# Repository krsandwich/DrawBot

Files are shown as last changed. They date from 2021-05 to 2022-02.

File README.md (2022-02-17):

# Drawbot

This is a parts list and assembly guide for the Lab64 drawbot, a small desktop robot that draws cool pictures for you. 

## Background 
The goal of this project is to build a desktop bot which can hold a pen and use it to draw images on a sheet of paper. Achieving this requires two main components -- the ability to move precisely in the XY plane over the paper, and the ability to lift a pen on and off of the paper. 

- **XY motion**
The XY motion is driven by two Nema-17 stepper motors, one mounted to each end of the x axis. [Here](https://www.youtube.com/watch?v=_nzxGOKhHSY ) is a visualization of how driving the stepper motors in sync and against each other allows the carriage to move in 3D.

- **Pen lifting**
The lifting of the pen is driven by a tiny SG90 servo. The pen will drop down by gravity when the servo is not blocking it. To lift the pen up, the servo rotates, lifting the pen-holder up and moving the pen off the paper. 

## Parts list

### Tools & Bolts
|  Item No  |  Qty / kit |  Description |  Link |
| :--- | :--- | :--- | :--- |
| 1 | 1 | Metric m5 allen key | [Amazon](https://www.amazon.com/Eklind-14610-Long-Hex-L-Key/dp/B000GAOAFK/)  |
| 2 | 1 | M5 bolt + nut set | [Amazon](https://www.amazon.com/DYWISHKEY-Pieces-Stainless-Steel-Button/dp/B07WZHN2XS/) |
| 3 | 12 | M5 t-nuts | [Amazon](https://www.amazon.com/100Pcs-T-Nuts-Carbon-Nickel-Plated-Sliding/) |

### Hardware
|  Item No  |  Qty / kit |  Description |  Link |
| :--- | :--- | :--- | :--- |
| 4 | 1 | Openbuilds 20x40x500 v-slot | [Openbuilds](https://openbuildspartstore.com/v-slot-20x40-linear-rail/) |
| 5 | 1 | Openbuilds 20x20x250 v-slot | [Openbuilds](https://openbuildspartstore.com/v-slot-20x20-linear-rail/) |
| 6 | 6 | V-slot wheels | [Amazon](https://www.amazon.com/AFUNTA-Plastic-Bearings-Printer-Compatible/dp/B07KPWJ3ZC/) |
| 7 | 5 | Bearings **could be 3d printable | [Amazon](https://www.amazon.com/gp/product/B07JMRR7CC/) |
| 8 | 1 | GT2 belt | [Amazon](https://www.amazon.com/Upgrade-Non-Slip-Abrasion-Resistance-Printers/dp/B08NVL55HC/) |

### Electronics
|  Item No  |  Qty / kit |  Description |  Link |
| :--- | :--- | :--- | :--- |
| 9 | 1 | Elegoo uno board | [Amazon](https://www.amazon.com/ELEGOO-Board-ATmega328P-ATMEGA16U2-Compliant/dp/B01EWOE0UU/) |
| 10 | 2 | Nema17 stepper motor | [Amazon](https://www.amazon.com/RTELLIGENT-Stepper-Bipolar-42x42x38mm-42A02C-XH2-54/dp/B0817TGDQM/?th=1) |
| 11 | 2 | A4988 stepper driver | [Amazon](https://www.amazon.com/ARCELI-Compatible-Stepper-StepStick-Controller/dp/B07MXXL2KW) |
| 12 | 1 | Towerpro micro servo | [Amazon](https://www.amazon.com/Smraza-Helicopter-Airplane-Control-Arduino/dp/B07L2SF3R4/ ) |
| 13 | 1 | Jumper wire | [Amazon](https://www.amazon.com/EDGELEC-Breadboard-Optional-Assorted-Multicolored/dp/B07GD431C1/) |
| 14 | 1 | Breadboard | [Amazon](https://www.amazon.com/Breadborad-Solderless-Breadboards-Distribution-Connecting/dp/B082VYXDF1/) |
| 15 | 2 | 9V battery | [Amazon](https://www.amazon.com/Energizer-Alkaline-Volt-Batteries-Count/dp/B01AVK3NMU/) |
| 16 | 2 | Battery hats | [Amazon](https://www.amazon.com/Battery-Connector-Leather-Housing-Connection/dp/B06X8YZJ64/) |

### 3D Prints
|  Item No  |  Qty / kit |  Description | 
| :--- | :--- | :--- |
| 17 | 2 | Stepper mount | 
| 18 | 2 | GT2 pulley for stepper | 
| 19 | 1 | Lower cart |
| 20 | 1 | Upper cart | 
| 21 | 4 | Cart spacers |
| 22 | 4 | Pulley spacers |
| 23 | 1 | Back pulley |
| 24 | 1 | Servo mount | 
| 25 | 1 | Pen mount |
| 26 | 1 | Belt clamp | 

## Mechanical Assembly

If you're coming here from the recent workshop, these instructions will be in a different order than you may remember. I recommend following these instructions from the start, and you may find that you've already done some steps as you go. 

These instructions may be difficult to follow in places -- I don't have enough photos, and don't have enough bolts to recreate the bot to take the photos. If you have trouble, we'll be having a second catcup-up mechanical session while people with the mechanics completed work on the electronics (electronics are far easier to complete on your own)

### Bolts
Your kit has the following bolts:
|  Item  |  Qty / kit |  Description | 
| :--- | :--- | :--- |
| M5 T-Nuts | 8 + 5 extra | Silvery oblong nuts with a hole in the middle | 
| M5 hex nuts | 7 + 5 extra | Hexagonal nuts with a hole in the middle | 
| M5x10 bolts | 8 | Shortest size |
| M5x12 bolts | 6 | Second-shortest (very hard to differentiate from M5x10s, be careful!) | 
| M5x16 bolts | 8 | Second-longest |
| M5x20 bolts | 6 OR 12 | Longest size |
| M5 allen key | 1 | Allen key used to screw in bolts |

Begin by sorting your bolts. It's okay if you have one more or less of each type.

### Stepper motor
Begin with the 2 Nema 17 stepper motors, 2 GT2 pulleys, and 2 stepper mounts (pictured below). To push the pulley onto the motor, look closely at the stepper motor axle and notice that they are not perfectly round, they have one flat edge. Line up that flat edge with the flat edge on the 3d printed pulley, flip the whole thing upside down, and push down hard against a flat object until the pulley is flush with the axle. Then, take the stepper mount. Orient the long side in the same direction as the stepper motor wires, and push until it snaps into place. It should hold without any screws. 

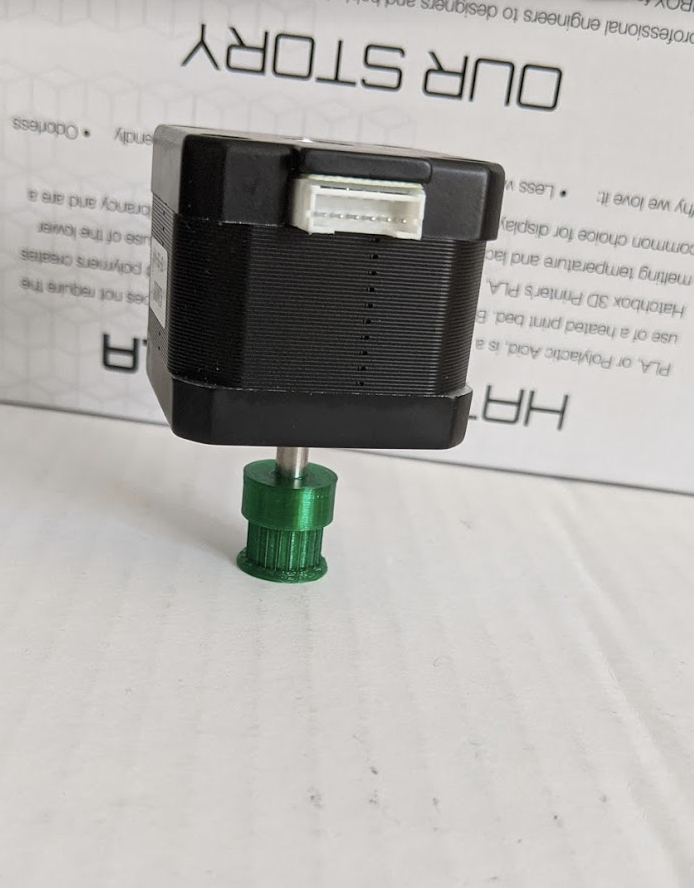
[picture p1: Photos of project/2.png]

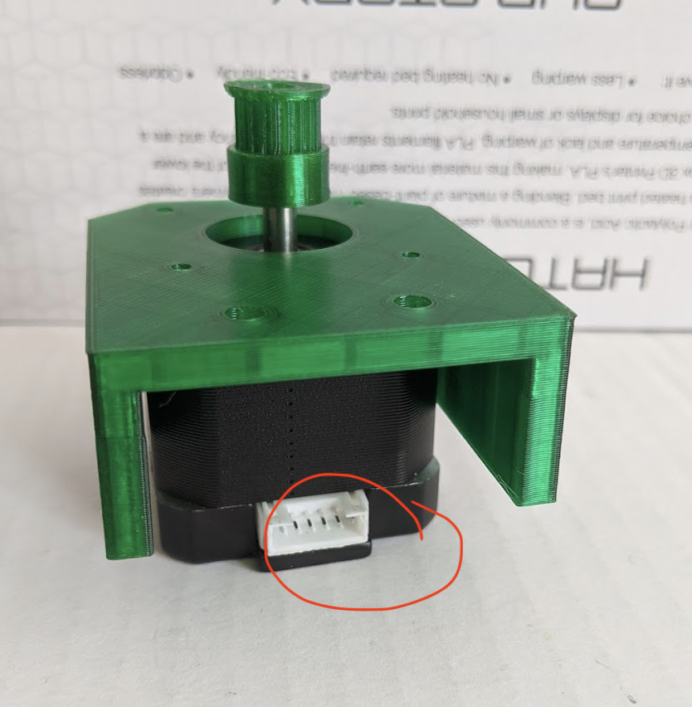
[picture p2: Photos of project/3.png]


### Main carriage
Select 6 M5x20s (20 mm long 5mm bolts), 6 M5 hex nuts, the black wheels, and the two round 3d printed carts. There are hexagonal holes on the insides of the carts, opposite the square lumps -- press the nuts in, they should snap into place. Flip the cart over and attach the wheels to the lumps with the M5x20s. You should leave the bolts just slightly loose; make sure that all wheels can spin freely.

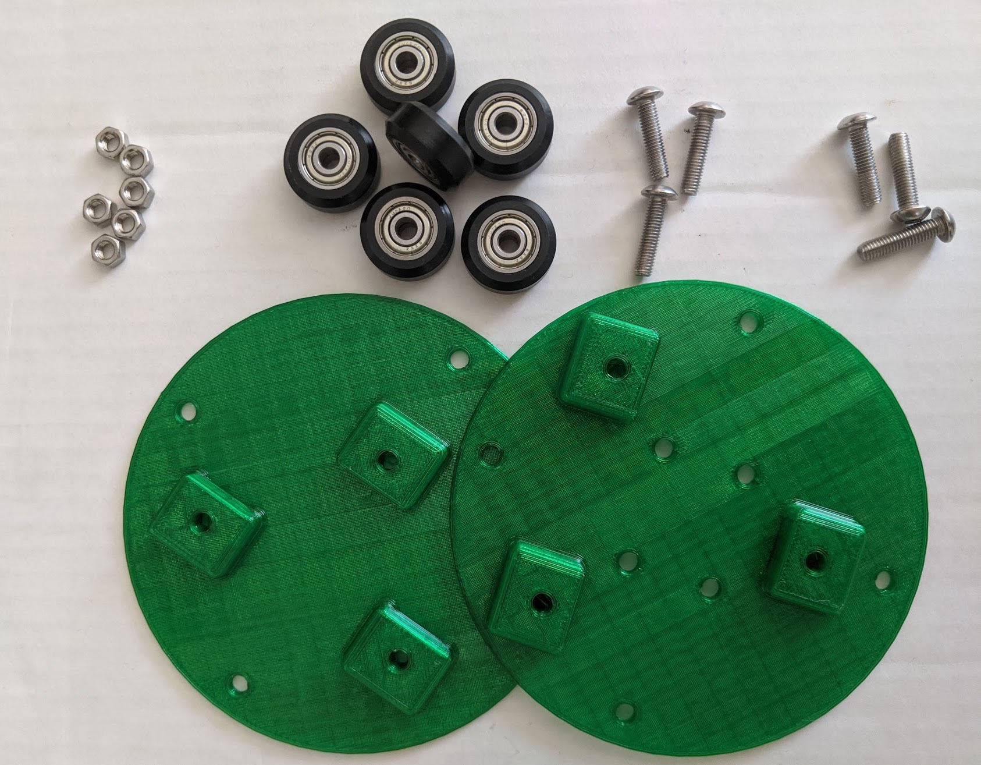
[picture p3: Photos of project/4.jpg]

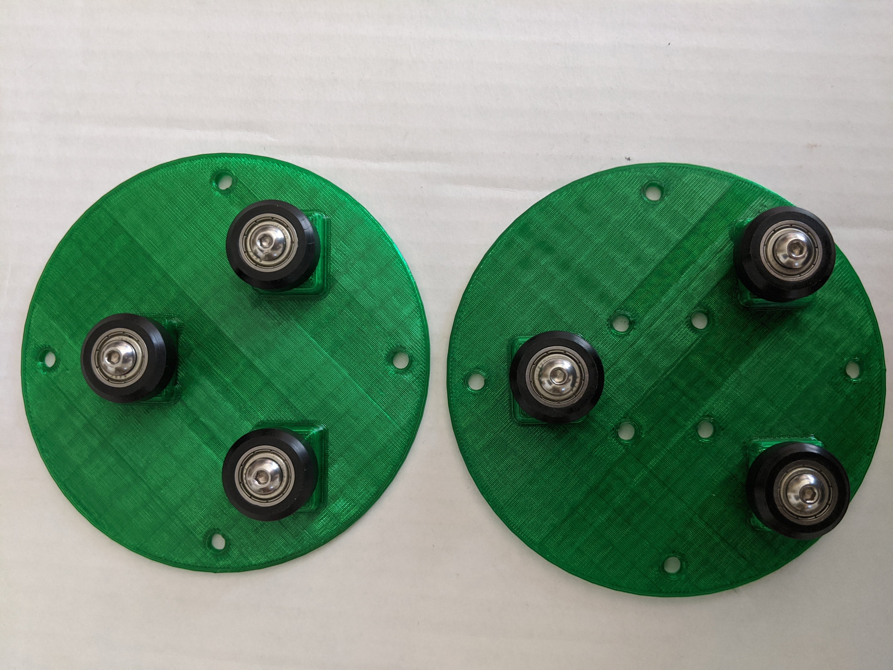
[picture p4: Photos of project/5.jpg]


One of the carts has four holes in the centre. The one with the holes is the lower cart, and the other is the upper cart. Take the lower cart, and insert four M5x12s through the center 4 holes, passing from the lumpy side to the inside (bolt head stays on the lumpy side). These will be used to hold pulleys. Slide the tiny spacers onto the M5x12s from the inside of the cart, with the slightly wider side down presing against it.  

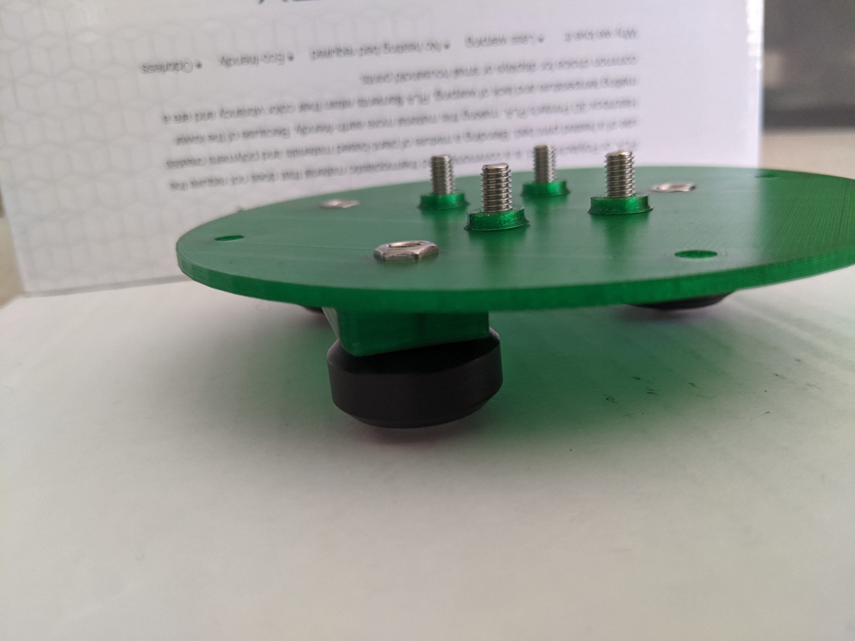
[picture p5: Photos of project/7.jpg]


Next, you will put in the spacers using four M5x16 bolts, as pictured. Once this is done, place the metal pulleys onto the middle M5x12s. You can then pick up the top cart and place it onto the bottom one. Tighten the M5x16s to connect. 

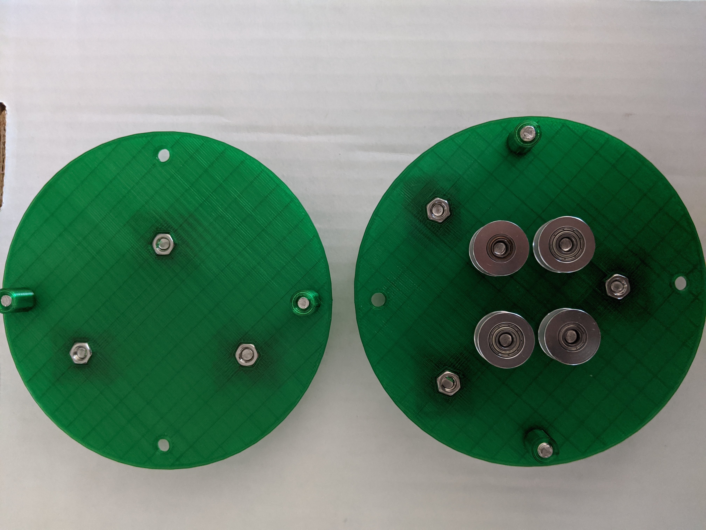
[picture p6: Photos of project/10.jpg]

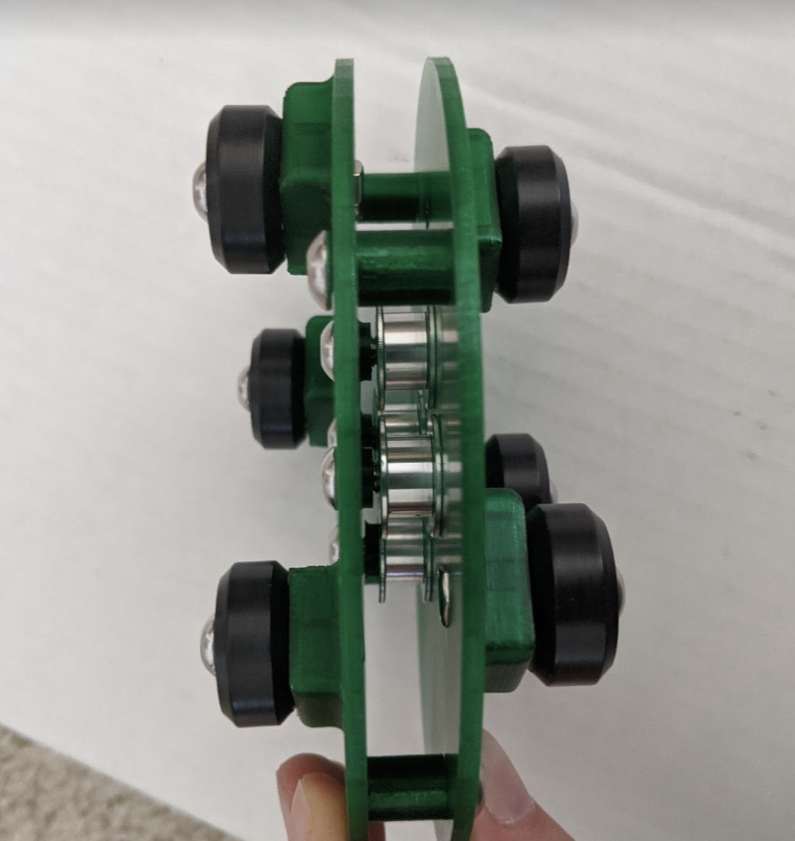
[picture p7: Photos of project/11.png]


### Attaching to metal
You will use small metal t-nuts in order to attach to the metal extrusion. The t-nuts will fit into the slots in the metal, and you will be able to put a M5x10 bolt through and tighten it to create a strong attachment. Begin with one of the stepper motors, and put two M5x10s through the holes. Then, thread the t-nuts ever-so-slightly on as pictured. Slide the larger piece of aluminum extrusion into the t-nuts, and tighten them down. They should create a firm attachment. If they do not, loosen them and try again -- it may take a few tries and some practice. When you're done, you will be able to shake pieces around and have it hold solidly without slipping at all. 

Then, you can roll the carriage onto the extrusion. Push the smaller piece of extrusion onto the upper cart. After the carriage is rolled onto the lower extrusion, you can attach the second stepper motor. 

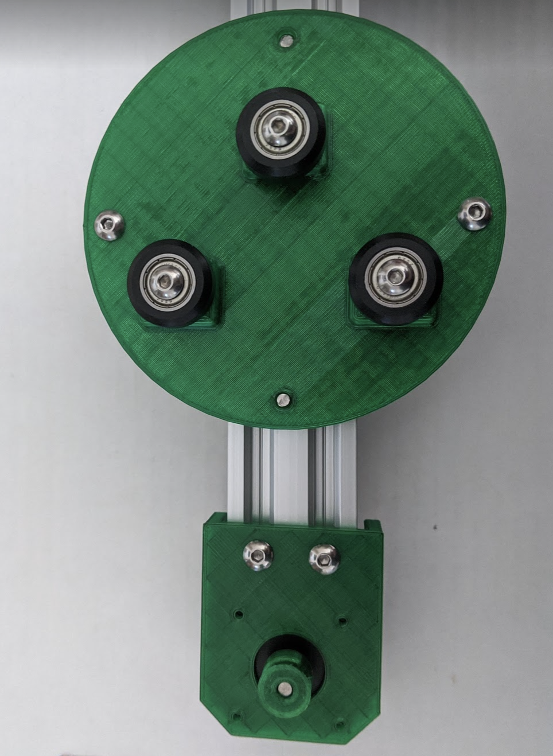
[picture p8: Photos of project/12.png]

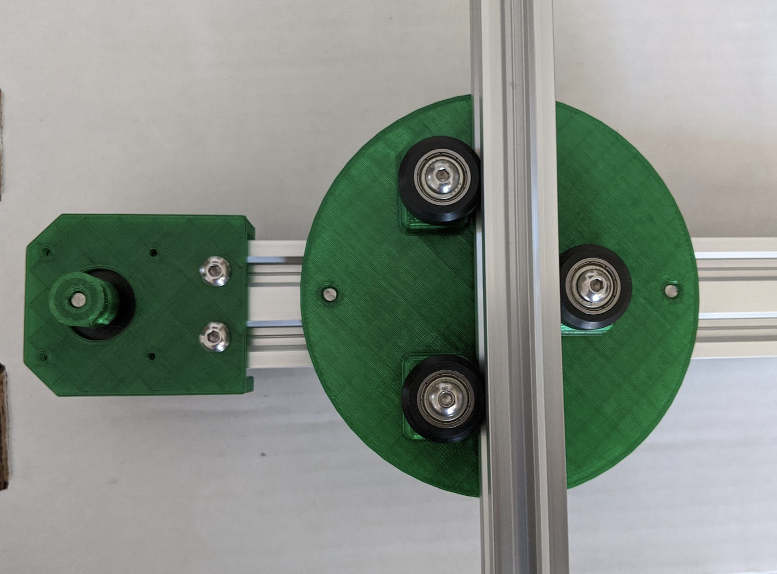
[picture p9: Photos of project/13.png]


### Attaching back pulley
Attach the last metal pulley to the U-shaped back pulley piece, with a M5x16 bolt passing loosely through the print from below up into the pulley. Then use the same strategy with the t-nuts and two M5x10s to attach the U-shaped back pulley piece to the small piece of metal extrusion. There are four potential holes you can use; I recommend just starting with two bolts diagonally across from each other. 
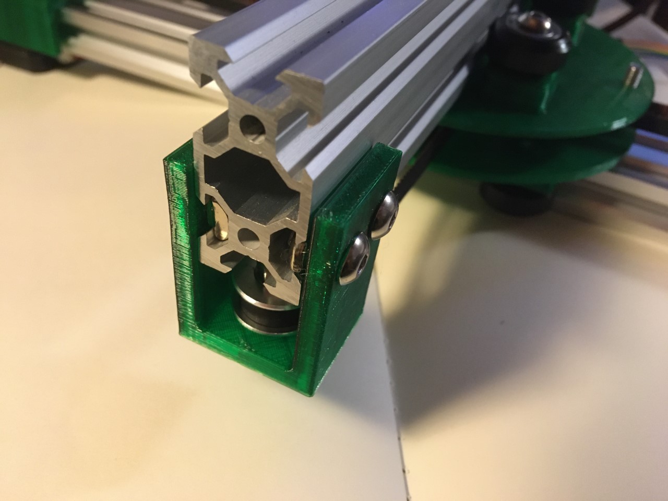
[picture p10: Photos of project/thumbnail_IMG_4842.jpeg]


### Pen mount
Begin by attaching the servo (in blue, in the photo) to the pen mount (in yellow). You can use the tiny pointy bolts that come with the servo bag, and use your fingers to tighten it as much as you can. Then affix the pen mount (in yellow) to the metal, using 2M5x10s, 2 t-nuts and the same procedure you just used for the back pulley. Next, you will run the belt, before completing the pen mount. 

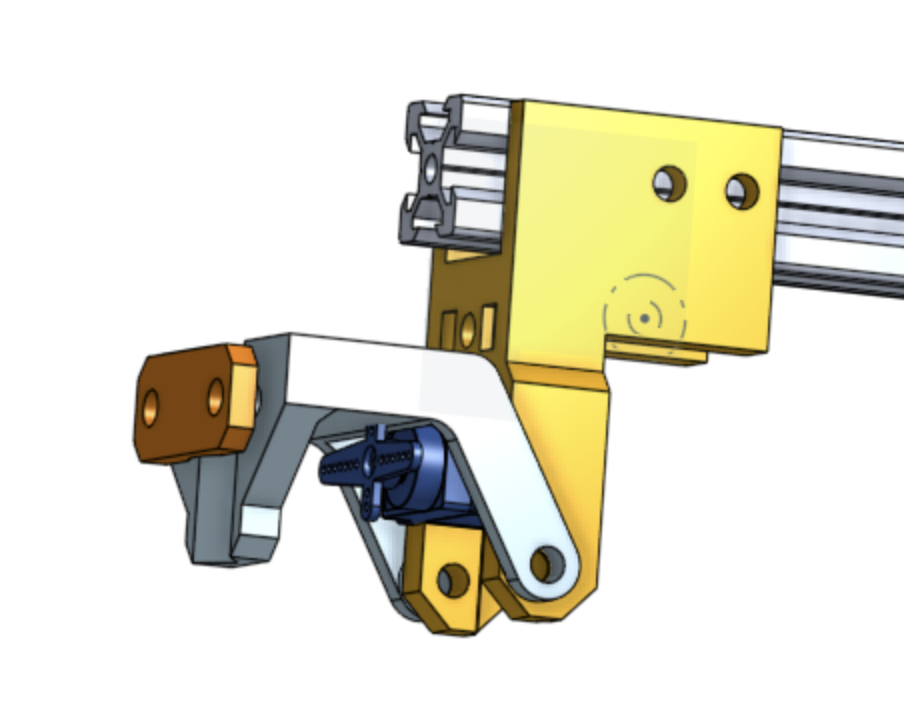
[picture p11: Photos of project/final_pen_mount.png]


### Running the belt
Running the belt is the trickiest part of the assembly. The belt must run around all of the pulleys in a plus sign, to transmit the motion of the steppers into the carriage. Begin by poking one end of the belt into the stepper mount. There are two parallel slots for the belt, slide one end through with the orientation shown in the diagram. Then cut a length of belt, and slide the opposite end into and out of the carriage in the pattern shown. I recommend getting chopsticks, tweezers, or a fork to grab the belt and move it aorund. If this does not work for you, undo the spacer bolts keeping the upper and lower cart together, loop the belt, and reassemble the carriage. Once you're done, pass it through the second slot in the stepper mount, and trim any extra. Tighten down the spiny piece using the center bolt to clamp the belt in place. 

If you hold the pulleys and twist them, the carriage should move. Moving the motors in the same direction will move the carriage left and right, and moving the motors in opposite directions will move the carriage back and forth. 

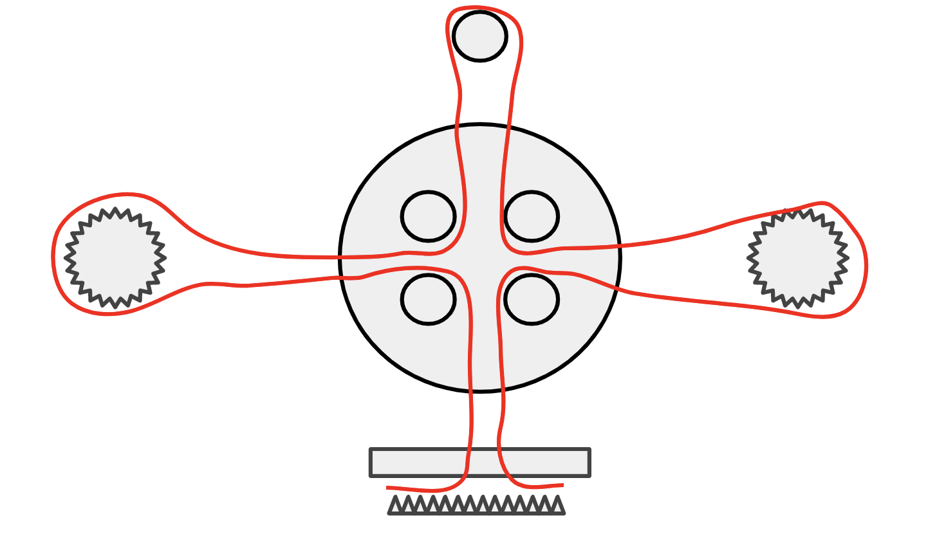
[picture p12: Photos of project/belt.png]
Belt diagram


### Attaching the pen
Attach the pen swivel (in light blue in the image in the Pen Mount section) to the pen mount, using 2 M5x12s. The swivel should be able to rotate up and down when the servo turns. Once you're sure that's in place, take any pencil. Clamp it to the pen swivel using 2 M5x16s, using the pen clamp (orange in the image). 

## Electronics

All electronics will be conected using the breadboard and jumper wires. This is a quick and easy way to prototype mechatronic systems. Full electronics photo TBD. 

### Stepper motors
Breadboards are connected horizontally. Gently push the red A4988 onto a breadboard, with each row of pins on a different half of the board. Make sure that the orientation matches the diagram, and link the wires as pictured. Repeat a second time for the second A4988 and second stepper motor, making sure to connect to pins 3&4 for the first and then 12&13 for the second on the elegoo. 
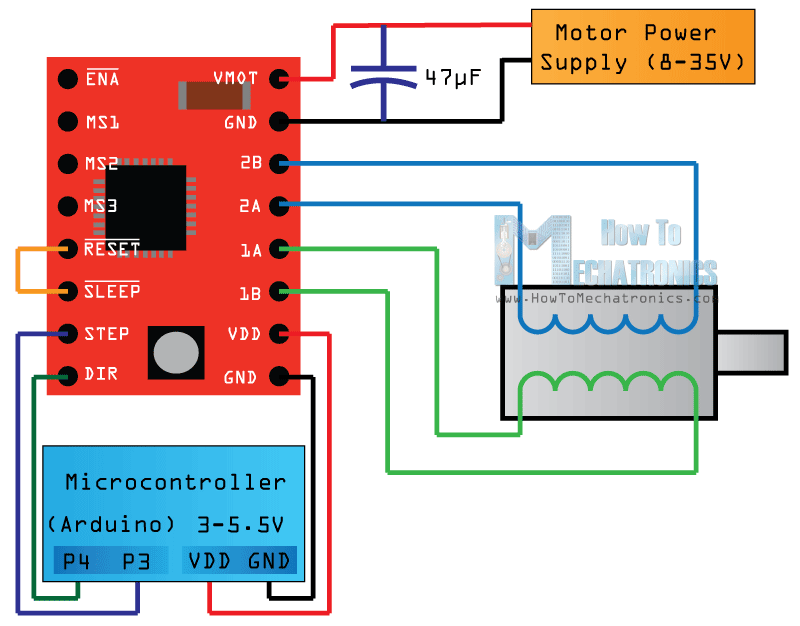
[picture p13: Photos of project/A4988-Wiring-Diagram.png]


### Servo
TBD.

## Code
The Elegoo board can be run directly from the Arduino software. Download the Arduino IDE here: https://www.arduino.cc/en/software

Test that your stepper motors are working by downloading the stepper test code from the "Starter Code" file. It should make your steppers run in a square, wait, and then do it again in an infinite loop. If your stepper motors are screaming and not rotating, please let us know and we can debug.

Now that you have that running, we will upload the real code. Please do the following: <br/>

`git clone https://github.com/krsandwich/DrawBot.git` <br/>
`cd DrawBot/drawbot_code` <br/>
`python3 -m venv .env` <br/>
`source .env/bin/activate` <br/>
`python3 -m pip install -r requirements.txt`<br/><br/>
Now, open drawbot_arduino and run the sketch making sure to specify the correct port for your arduino. Copy down the port name and put it in line 73 of drawbot.py. Now run the following command:<br/><br/>
`
python3 drawbot.py
`<br/><br/>
You will see a hello world graphic pop up! The black lines represent lines that will be drawn and red lines represent movement. Make sure your motors are connected to power (you should hear an annoying buzz) and that the arduino script is running. Now you can close the Hello World window and the drawbot should start drawing!

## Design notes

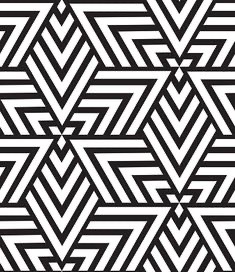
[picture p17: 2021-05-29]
drawbot_code/imgs/lines.jpg

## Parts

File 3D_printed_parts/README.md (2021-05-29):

### 3D Printed Parts



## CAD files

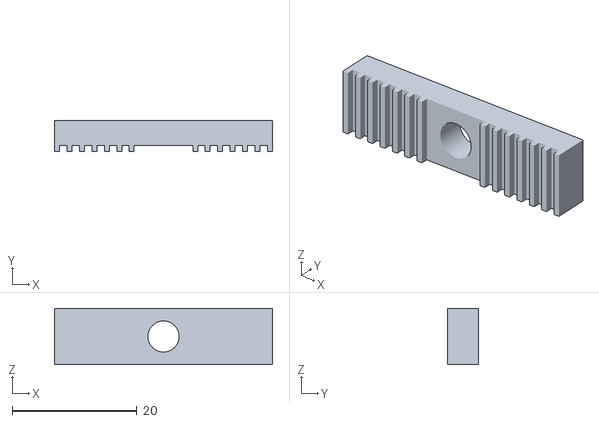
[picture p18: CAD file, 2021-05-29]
3D_printed_parts/GT2_belt_clamp.stl
35.0 x 5.00 x 9.00

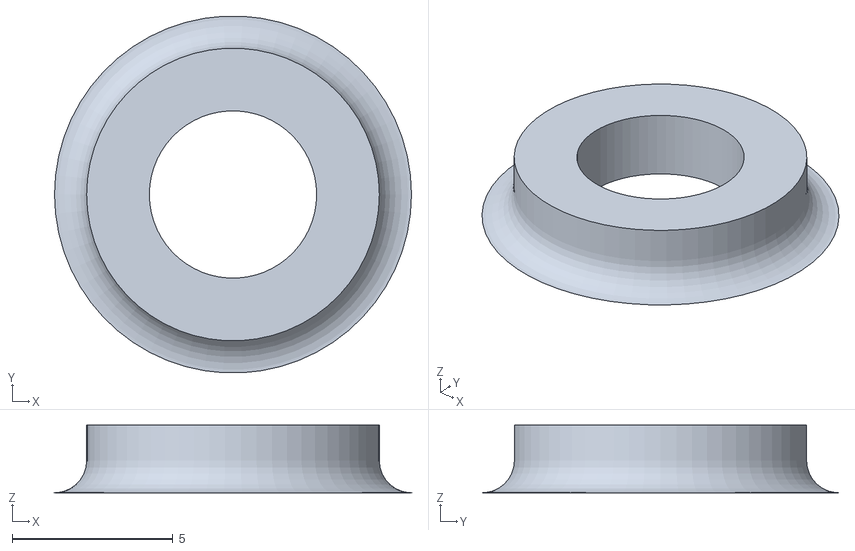
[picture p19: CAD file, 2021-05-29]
3D_printed_parts/Pulley_spacer.stl
11.1 x 11.1 x 2.10

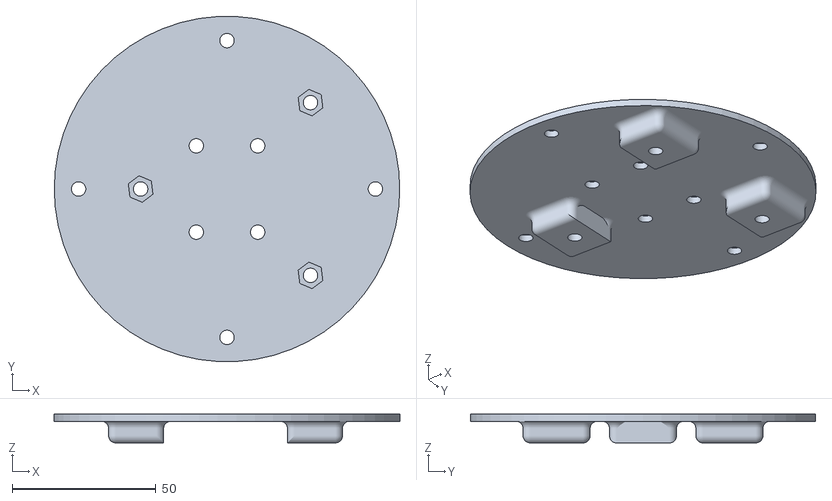
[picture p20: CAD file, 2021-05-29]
3D_printed_parts/Lower_cart.stl
120.0 x 119.8 x 10.0

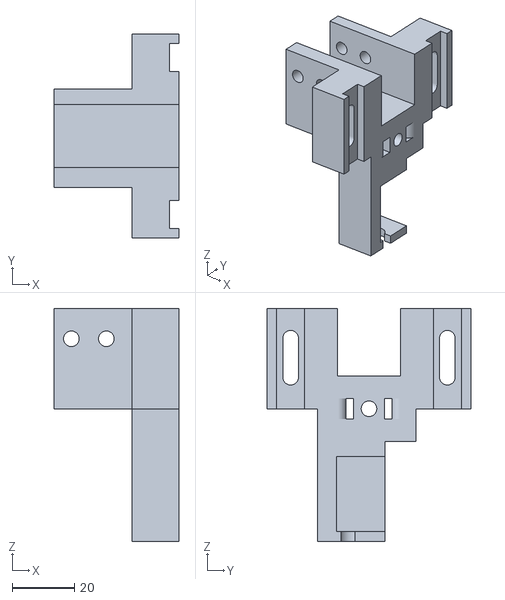
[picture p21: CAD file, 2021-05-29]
3D_printed_parts/Servo_mount.stl
40.0 x 65.2 x 74.6

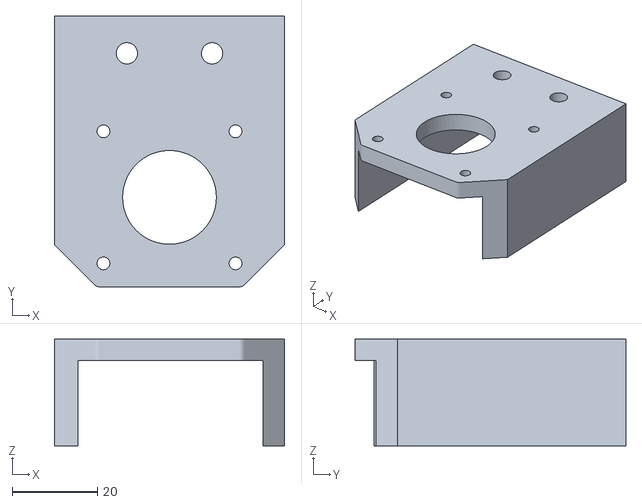
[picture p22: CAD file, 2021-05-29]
3D_printed_parts/Stepper_clamp.stl
54.0 x 63.5 x 25.0

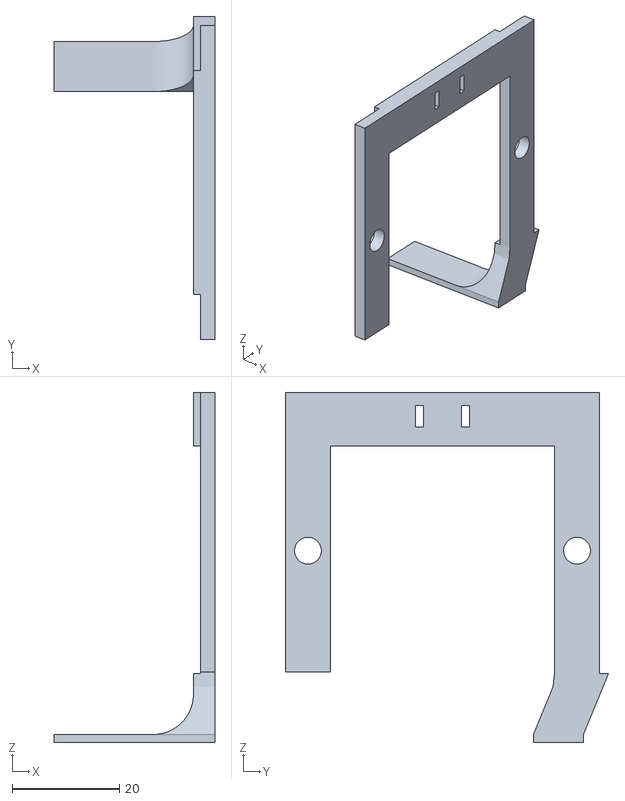
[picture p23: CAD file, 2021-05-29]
3D_printed_parts/Pen_Mount.stl
30.0 x 60.3 x 65.3

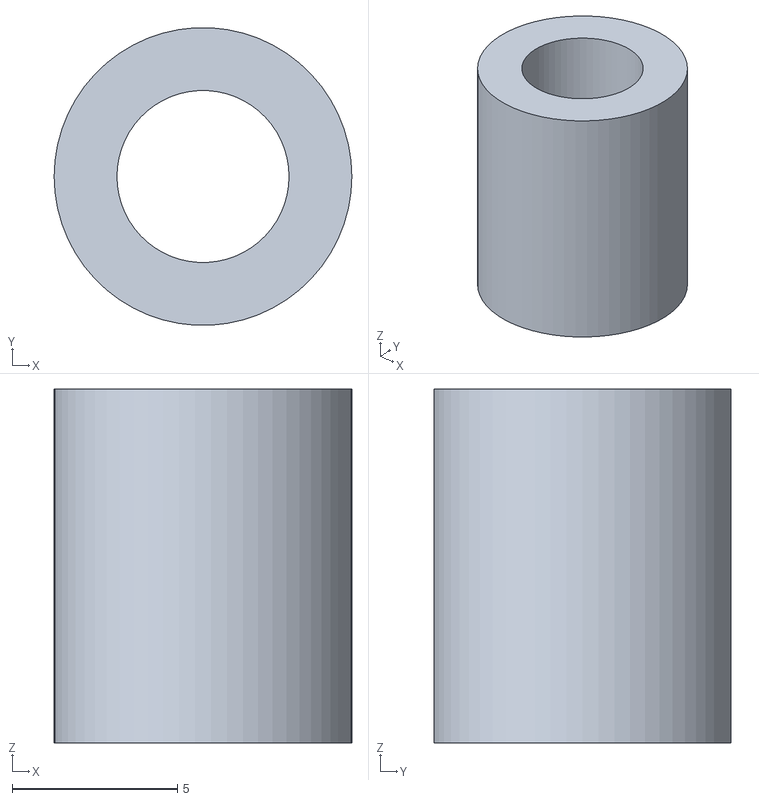
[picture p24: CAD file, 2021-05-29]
3D_printed_parts/Spacer.stl
9.00 x 8.99 x 10.7

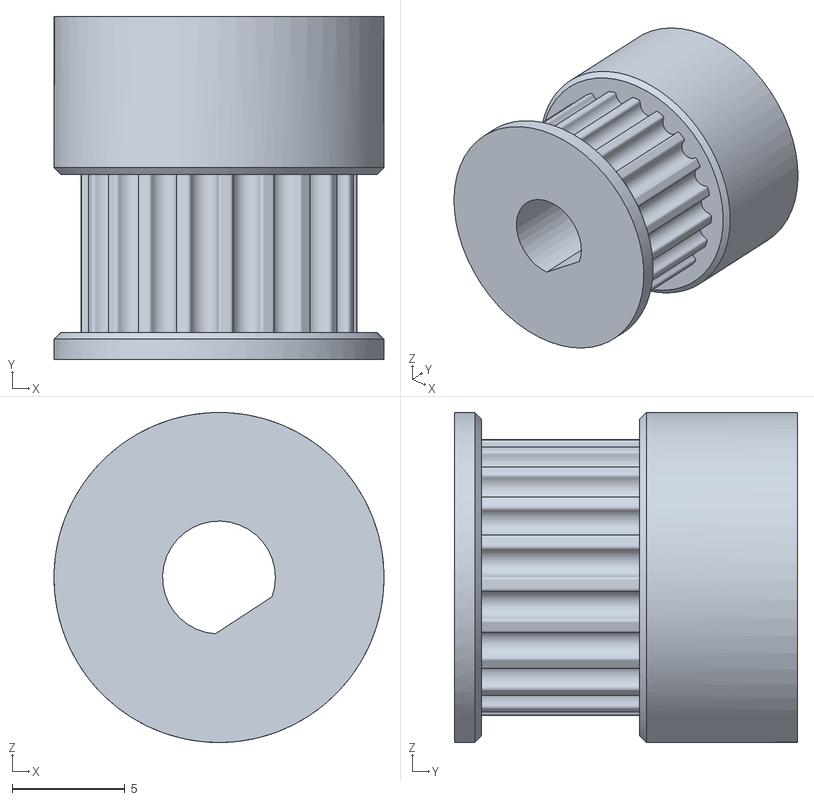
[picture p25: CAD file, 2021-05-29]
3D_printed_parts/GT2_Pulley.stl
14.6 x 15.2 x 14.6

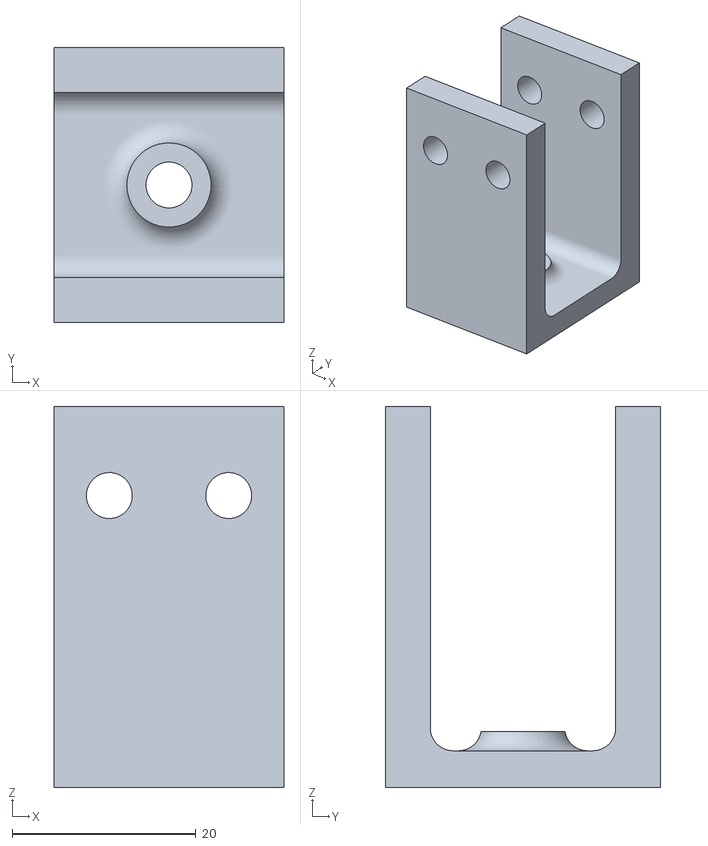
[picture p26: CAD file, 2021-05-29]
3D_printed_parts/Back_pulley.stl
25.0 x 30.0 x 41.5

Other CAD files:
3D_printed_parts/Upper_cart.stl

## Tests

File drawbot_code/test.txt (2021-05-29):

m 20.92268,117.88144 c 0.36974,-0.22427 -0.222948,-3.41363 0,-4.08247 0.07607,-0.22822 0.510309,-0.26975 0.510309,-0.51031 0,-0.24056 -0.510309,-0.26975 -0.510309,-0.51031 0,-0.16455 0.878846,-0.73707 1.020619,-1.02062 0.07607,-0.15214 -0.05379,-0.34893 0,-0.51031 0.124309,-0.37293 0.553521,-1.29738 1.020618,-1.53093 0.114376,-0.0572 1.919972,0 2.041237,0 0.170104,0 -0.680412,0 -0.510309,0 0.340206,0 0.780057,-0.24056 1.020619,0 0.170103,0.17011 -0.568655,0.27693 -0.51031,0.51031 0.516023,2.0641 1.530929,0.87402 1.530929,3.06186 0,0.86736 -0.402727,1.69088 -0.51031,2.55154 -0.0633,0.50637 0,1.02062 0,1.53093 0,1.02062 0,2.04124 0,3.06186 0,3.91237 0,7.82474 0,11.73711 0,0.85052 0,1.70103 0,2.55155 0,0.51031 0.0633,1.02456 0,1.53093 -0.107583,0.86066 -0.299944,1.71008 -0.510309,2.55154 -0.130464,0.52186 -0.44359,0.99717 -0.51031,1.53093 -0.105493,0.84395 0.08463,1.70525 0,2.55154 -0.0863,0.86306 -0.402726,1.69089 -0.510309,2.55155 -0.0633,0.50637 0.123768,1.03586 0,1.53093 -0.222171,0.88868 -0.798448,1.66286 -1.020619,2.55155 -0.123768,0.49507 0,1.02061 0,1.53092 -0.170103,0.51031 -0.340206,1.02062 -0.510309,1.53093 -0.363509,1.09053 -0.860425,2.45081 -1.020618,3.57217 -0.04474,0.3132 0.119786,3.33259 0,3.57216 -0.215166,0.43033 -0.753739,0.6203 -1.020619,1.02062 -0.09436,0.14154 0.05379,0.34893 0,0.51031 -0.120281,0.36084 -0.510309,0.64026 -0.510309,1.02062 0,0.24056 0.402727,0.29514 0.510309,0.51031 0.405643,0.81128 -1.020618,1.05151 -1.020618,1.53093 0,0.1701 0.340206,0 0.510309,0 0,0.3402 0.152145,0.71632 0,1.02061 -0.07607,0.15215 -0.390028,-0.12028 -0.510309,0 -0.120281,0.12028 0,0.68042 0,0.51031 0,-2.69548 -0.360843,-0.7345 0.510309,-2.04123 0.210987,-0.31649 0.282092,-0.71633 0.510309,-1.02062 3.384966,-3.38497 -0.481124,0.96225 1.020619,-2.04124 0.215165,-0.43033 0.841933,-0.57391 1.020618,-1.02062 0.189524,-0.47381 -0.189524,-1.05712 0,-1.53093 0.830745,-0.83074 1.168191,-0.95302 1.530928,-2.04123 0.221787,-0.66536 0.149466,-1.43983 0.510309,-2.04124 0.195695,-0.32616 0.928368,-0.1413 1.020619,-0.51031 0.130463,-0.52185 -0.680412,-1.02062 -0.510309,-1.53093 0.228217,-0.68465 1.20818,-0.88543 1.530927,-1.53093 0.228219,-0.45643 -0.262552,-1.09334 0,-1.53092 0.31555,-0.52592 1.162939,-0.52997 1.530929,-1.02062 0.204123,-0.27217 -0.08251,-0.69057 0,-1.02062 0.09225,-0.36901 0.340207,-0.68041 0.51031,-1.02062 1.850017,-3.70004 -0.537914,0.80687 1.020617,-1.53093 0.210986,-0.31648 0.241353,-0.75166 0.51031,-1.02062 0.268957,-0.26895 0.704138,-0.29932 1.020619,-0.51031 0.600477,-0.40031 0.953577,-1.09791 1.530927,-1.53092 0.304289,-0.22822 0.704138,-0.29933 1.020617,-0.51031 0.170103,-0.1701 0.340207,-0.34021 0.51031,-0.51031 0,-0.1701 -0.12028,-0.39003 0,-0.51031 0.120282,-0.12028 0.358166,0.0761 0.51031,0 0.215164,-0.10758 0.295145,-0.40273 0.510309,-0.51031 0.152144,-0.0761 0.340207,0 0.51031,0 0.340207,0 0.680411,0 1.020617,0 0.170103,0 -0.68041,0 -0.51031,0 0.340207,0 0.680413,0 1.02062,0 0.170103,0 -0.680413,0 -0.51031,0 0.340207,0 0.680413,0 1.02062,0 0.170103,0 -0.390028,-0.12028 -0.51031,0 -0.12028,0.12028 0,0.34021 0,0.51031 0,1.19072 0,2.38144 0,3.57216 0,4.42268 0,8.84537 0,13.26805 0,2.04123 0,4.08247 0,6.12371 0,0.68041 0.08439,1.36608 0,2.04124 -0.08699,0.69593 -0.411123,1.34693 -0.51031,2.04123 -0.07217,0.50518 0.08389,1.02756 0,1.53093 -0.08843,0.53059 -0.404815,1.00346 -0.51031,1.53093 -0.133437,0.6672 0,1.36082 0,2.04123 0,0.85052 0,1.70103 0,2.55155 0,0.34021 0,1.36082 0,1.02062 0,-0.34021 -0.152143,-0.71633 0,-1.02062 0.430332,-0.86066 1.50748,-1.2406 2.04124,-2.04124 0.421973,-0.63296 0.643194,-1.38074 1.020617,-2.04123 0.304289,-0.53251 0.746336,-0.98237 1.020619,-1.53093 0.240562,-0.48113 0.269748,-1.0498 0.51031,-1.53093 0.613315,-1.22663 1.375219,-2.37333 2.041237,-3.57216 0.184718,-0.3325 0.314613,-0.69446 0.510309,-1.02062 0.315548,-0.52592 0.805268,-0.95667 1.020617,-1.53093 0.873438,-2.32916 0.07625,-2.19374 1.02062,-4.08247 0.443574,-0.88715 1.005242,-1.71045 1.530927,-2.55155 0.325056,-0.52009 0.900337,-0.92952 1.020619,-1.53093 0.07459,-0.37297 -0.630589,-0.65978 -0.51031,-1.02062 0.268957,-0.80687 1.150568,-1.28051 1.530927,-2.04123 0.304292,-0.60858 -0.304289,-1.43266 0,-2.04124 0.215167,-0.43033 0.75374,-0.6203 1.02062,-1.02062 0.09436,-0.14154 0,-0.34021 0,-0.51031 0,-0.1701 0,-0.34021 0,-0.51031 0,-0.1701 0,-0.34021 0,-0.51031 0,-0.1701 0.152146,-0.43424 0,-0.51031 -0.456435,-0.22821 -1.02062,0 -1.530927,0 -0.167587,0 -1.454893,-0.0507 -1.530929,0 -1.991204,1.32747 -0.504413,0.49262 -1.020617,2.04124 -0.388477,1.16543 -1.02062,-0.31544 -1.02062,1.53093 0,0.24056 0.51031,0.26975 0.51031,0.51031 0,0.38036 -0.418058,0.65161 -0.51031,1.02062 -0.08251,0.33004 0,0.68041 0,1.02061 0,0.51031 0,1.02062 0,1.53093 0,1.53093 0,3.06186 0,4.59279 0,0.32615 -0.0736,2.91465 0,3.06185 0.51031,1.02062 1.02062,0.76547 1.530927,1.53093 0.869294,1.30394 0.05944,0.93762 1.530929,2.04124 0.608579,0.45643 1.432658,0.56418 2.041237,1.02062 0.340206,0.3402 0.680413,0.68041 1.020619,1.02061 0.170104,0 0.358164,-0.0761 0.510308,0 0.215167,0.10758 0.282093,0.43424 0.510309,0.51031 0.32275,0.10758 0.716331,-0.15214 1.02062,0 0.152143,0.0761 -0.120282,0.39003 0,0.51031 0.12028,0.12028 0.390028,-0.12028 0.51031,0 0.120279,0.12028 -0.120282,0.39003 0,0.51031 0.120279,0.12028 0.340206,0 0.510307,0 0.850516,0 1.701033,0 2.551546,0 0.170104,0 0.390031,0.12028 0.51031,0 0.268957,-0.26896 0.241353,-0.75166 0.51031,-1.02062 0.268957,-0.26895 0.751663,-0.24135 1.02062,-0.51031 0.537911,-0.53791 0.545396,-1.44721 1.020617,-2.04123 0.450834,-0.56355 1.159623,-0.91209 1.530929,-1.53093 0.175032,-0.29173 -0.134014,-0.70792 0,-1.02062 0.390713,-0.91167 1.005239,-1.71045 1.530927,-2.55155 0.325056,-0.52009 0.80527,-0.95666 1.020619,-1.53092 0.304549,-0.81214 0.255231,-1.72255 0.510308,-2.55155 0.427413,-1.38909 1.009202,-2.72599 1.530929,-4.08248 0.328837,-0.85497 0.78459,-1.66644 1.020617,-2.55154 3.545901,-13.29713 -0.812115,1.47793 1.530929,-8.67526 0.241909,-1.04827 0.583684,-2.07875 1.020617,-3.06185 0.249092,-0.56046 0.919793,-0.92596 1.02062,-1.53093 0.420402,-2.52242 0.288779,-5.10704 0.51031,-7.65464 0.118806,-1.36626 0.35007,-2.72045 0.51031,-4.08248 0.539377,-4.5847 1.147516,-9.17742 1.530926,-13.77835 0.02825,-0.33903 0,-0.68041 0,-1.02061 0,-1.70103 0,-3.40207 0,-5.1031 0,-2.04123 0,-4.082471 0,-6.12371 0,-0.08755 0.06238,-2.874724 0,-3.061854 -0.338497,-1.015489 -0.476289,-0.238146 -1.020619,-0.510309 -0.215165,-0.107583 -0.295143,-0.402728 -0.510307,-0.51031 -0.08165,-0.04082 -1.510517,-0.04082 -1.53093,0 -0.152143,0.304289 0.175035,0.728895 0,1.020619 -0.371303,0.61884 -1.20818,0.885431 -1.530927,1.530927 -0.228219,0.456436 0.140193,1.040255 0,1.530927 -1.560113,5.4604 -0.568679,-0.757952 -1.530929,3.57217 -0.224457,1.01005 -0.238062,2.06361 -0.510307,3.06185 -0.241025,0.88376 -0.856755,1.65029 -1.02062,2.55155 -0.182573,1.00415 0.0924,2.04543 0,3.06185 -0.07852,0.8638 -0.438279,1.68719 -0.51031,2.55155 -0.09888,1.18661 0,2.38144 0,3.57216 0,0.85052 0,1.70104 0,2.55155 0,4.25258 0,8.50516 0,12.75773 0,4.76289 0,9.52578 0,14.28866 0,0.85052 0,1.70103 0,2.55155 0,0.85051 -0.233653,1.73375 0,2.55155 0.132176,0.46261 0.805453,0.59028 1.02062,1.02061 1.248024,1.00321 0.0636,2.45539 0.51031,3.57217 0.178684,0.44671 0.805452,0.59029 1.020617,1.02062 0.304289,0.60858 -0.377426,1.4751 0,2.04124 0.210986,0.31647 0.850516,0.1701 1.020619,0.5103 0.107583,0.21517 -0.340206,0.34021 -0.510309,0.51031 0.340206,0.17011 0.751662,0.24136 1.020619,0.51031 0.240562,0.24056 -0.152146,0.71633 0,1.02062 0.194239,0.38848 1.220153,1.02062 1.530927,1.02062 0.240562,0 -0.51031,-0.75087 -0.51031,-0.51031 0,0.004 0.632143,1.53093 1.02062,1.53093 0.255153,0 -0.680413,-2.21134 1.020617,-0.51031 0.170103,0.1701 -0.510307,0.26975 -0.510307,0.51031 0,0.1701 0.340203,0 0.510307,0 0.51031,0 1.020619,0 1.530929,0 0.51031,0 1.020617,0 1.530927,0 0.340206,0 0.831905,0.28307 1.02062,0 0.283067,-0.4246 -0.228219,-1.0745 0,-1.53093 0.170103,-0.34021 0.783007,-0.2133 1.020617,-0.51031 0.47522,-0.59402 0.680413,-1.36082 1.020619,-2.04124 0.850516,-0.68041 1.842709,-1.21426 2.551546,-2.04123 0.350071,-0.40842 0.24343,-1.06389 0.51031,-1.53093 0.43052,-1.6729 2.230673,-2.24227 3.061856,-3.57217 0.485495,-0.77679 0.610955,-1.73222 1.020617,-2.55154 0.274283,-0.54857 0.722768,-0.9948 1.02062,-1.53093 0.464047,-0.83529 2.292466,-4.44754 2.551546,-5.6134 0.147601,-0.66421 -0.07514,-1.36499 0,-2.04124 0.269688,-2.42719 1.228014,-4.72101 1.530927,-7.14433 0.0633,-0.50637 0,-1.02062 0,-1.53093 0,-0.85051 0,-1.70103 0,-2.55154 0,-1.87114 0,-3.74227 0,-5.61341 0,-0.45607 0.08131,-2.38892 0,-2.55154 -0.209896,-0.41979 -1.789626,-1.66382 -2.041236,-2.04124 -0.09436,-0.14153 0.07607,-0.35816 0,-0.51031 -0.340207,-0.51031 -0.680413,-1.02062 -1.02062,-1.53093 -0.170103,0 -0.390028,0.12029 -0.510307,0 -0.120282,-0.12028 0.09436,-0.36877 0,-0.51031 -0.26688,-0.40032 -0.6203,-0.75373 -1.02062,-1.02061 -0.141533,-0.0944 -0.51031,0.1701 -0.51031,0 0,-2.46176 1.152909,-0.44417 0,-1.02062 -0.215164,-0.10758 -0.269748,-0.51031 -0.510309,-0.51031 -0.170104,0 0.120282,0.39003 0,0.51031 -0.240562,0.24056 -0.780056,-0.24056 -1.020617,0 -2.379808,2.3798 -0.371356,0.60376 -1.02062,2.55154 -1.72571,5.17713 -0.17285,-0.20782 -2.041237,3.06186 -4.60299,8.05523 0.676035,-1.25607 -0.510309,4.08247 -0.247537,1.11392 -1.067488,2.01912 -1.530927,3.06186 -0.765855,1.72317 -0.55971,2.51869 -1.02062,4.59278 -0.116689,0.52511 -0.44359,0.99717 -0.510309,1.53093 -0.105493,0.84395 0,1.70103 0,2.55155 0,0.85051 0,1.70103 0,2.55154 0,3.06186 0,6.12371 0,9.18557 0,2.21134 0,4.42268 0,6.63402 0,0.34021 0,0.68041 0,1.02062 0,0.34021 -0.152144,0.71633 0,1.02062 0.215167,0.43033 0.731945,0.63572 1.020619,1.02062 0.591222,0.78829 0.964404,2.21207 1.530927,3.06185 0.13344,0.20016 0.37687,0.31015 0.51031,0.51031 0.210986,0.31648 0.299323,0.70414 0.510309,1.02062 0.13344,0.20016 0.340207,0.34021 0.51031,0.51031 0.170104,0.1701 0.269746,0.51031 0.51031,0.51031 0.240562,0 0.340204,-0.68041 0.510307,-0.51031 0.240562,0.24056 -0.304289,0.86847 0,1.02062 0.340207,0.1701 0.659776,-0.63059 1.02062,-0.51031 0.360844,0.12028 0.241353,0.75166 0.51031,1.02062 0.120279,0.12028 0.348935,-0.0538 0.510309,0 0.360842,0.12028 0.640255,0.51031 1.020617,0.51031 0.240562,0 0.282094,-0.43424 0.51031,-0.51031 0.484122,-0.16138 1.02062,0 1.530927,0 0.850516,0 1.701033,0 2.551546,0 2.891753,0 5.783506,0 8.675259,0 0.51031,0 1.020621,0 1.530931,0 0.1701,0 0.39003,0.12028 0.51031,0 0.26895,-0.26896 0.1701,-0.85052 0.51031,-1.02062 0.21516,-0.10758 0.29514,0.61789 0.51031,0.51031 0.3402,-0.1701 0.24135,-0.75166 0.5103,-1.02062 0.12028,-0.12028 0.35817,0.0761 0.51031,0 0.58503,-0.29251 0.70985,-1.06477 1.02062,-1.53093 0.39255,-0.58882 1.13838,-0.94211 1.53093,-1.53093 1.71866,-2.57798 0.004,-0.0118 0.51031,-1.53092 -0.30758,-0.92363 0.82667,-0.94909 1.02062,-1.53093 0.10758,-0.32275 -0.0825,-0.69057 0,-1.02062 0.0922,-0.36901 0.41806,-0.65161 0.51031,-1.02062 0.0825,-0.33005 0,-0.68041 0,-1.02062 0,-0.3402 0,-0.68041 0,-1.02062 0,-1.02061 0,-2.04123 0,-3.06185 0,-1.19072 0,-2.38145 0,-3.57217 0,-0.1701 0.12028,-0.39002 0,-0.51031 -0.26896,-0.26895 -0.70414,-0.29932 -1.02062,-0.51031 -0.20016,-0.13344 -0.29515,-0.40272 -0.51031,-0.51031 -0.15214,-0.0761 -0.39003,0.12029 -0.51031,0 -0.004,-0.004 -0.62983,-1.53092 -1.02062,-1.53092 -0.24056,0 -0.29514,0.61789 -0.51031,0.51031 -0.3402,-0.17011 -0.1701,-0.85052 -0.51031,-1.02062 -0.21516,-0.10758 -0.29514,0.40273 -0.51031,0.51031 -0.15214,0.0761 -0.3402,0 -0.51031,0 -0.1701,0 -0.3402,0 -0.5103,0 -0.24061,0 -2.528424,-0.0231 -2.551551,0 -0.268957,0.26896 -0.340207,0.68041 -0.51031,1.02062 -0.170103,0.3402 -0.418057,0.65161 -0.51031,1.02061 -0.165023,0.6601 0.165024,1.38115 0,2.04124 -0.09225,0.36901 -0.447778,0.64543 -0.510309,1.02062 -0.111858,0.67116 0,1.36082 0,2.04124 0,1.19072 0,2.38144 0,3.57216 0,1.70103 0,3.40206 0,5.1031 0,0.44222 -0.09854,1.74562 0,2.04123 0.750149,2.25045 0.05671,0.53867 1.020619,1.02062 0.72249,0.36125 0.29813,0.65938 1.020621,1.02062 0.15214,0.0761 0.39003,-0.12028 0.51031,0 0.004,0.004 0.62983,1.53093 1.02062,1.53093 0.24056,0 0.29514,-0.61789 0.51031,-0.51031 0.3402,0.1701 0.1701,0.85051 0.5103,1.02062 0.21517,0.10758 0.29515,-0.6179 0.51031,-0.51031 0.34021,0.1701 0.17011,0.85051 0.51031,1.02062 0.21517,0.10758 0.34021,-0.68042 0.51031,-0.51031 0.24056,0.24056 -0.24056,0.78005 0,1.02062 0.17011,0.1701 0.29514,-0.40273 0.51031,-0.51031 0.15215,-0.0761 0.34021,0 0.51031,0 0.1701,0 0.34021,0 0.51031,0 0.51031,0 1.02062,0 1.53093,0 0.1701,0 -0.68041,0 -0.51031,0 0.3402,0 0.68041,0 1.02062,0 0.1701,0 0.43423,0.15214 0.51031,0 0.15214,-0.30429 -0.15215,-0.71633 0,-1.02062 0.0761,-0.15215 0.35816,0.0761 0.5103,0 0.21517,-0.10759 0.34021,-0.34021 0.51031,-0.51031 0.17011,-0.1701 0.40273,-0.29515 0.51031,-0.51031 0.0761,-0.15215 -0.0538,-0.34894 0,-0.51031 1.23213,-3.69638 -0.14712,0.80456 1.02062,-1.53093 0.0761,-0.15214 0,-0.3402 0,-0.51031 0,-0.1701 0,-0.3402 0,-0.51031 0,-0.68041 0,-1.36082 0,-2.04123 0,-0.22983 0.0777,-1.37563 0,-1.53093 -0.27428,-0.54857 -0.74633,-0.98236 -1.02062,-1.53093 -0.0761,-0.15214 0.12028,-0.39003 0,-0.51031 -0.43368,-0.43368 -1.16293,-0.52997 -1.53092,-1.02062 -0.20413,-0.27216 0.10758,-0.69787 0,-1.02062 -0.0761,-0.22821 -0.37687,-0.31015 -0.51031,-0.51031 -0.21099,-0.31647 -0.29933,-0.70413 -0.51031,-1.02061 -0.13344,-0.20016 -0.37687,-0.31015 -0.51031,-0.51031 -0.21099,-0.31648 -0.29932,-0.70414 -0.51031,-1.02062 -0.13344,-0.20016 -0.40273,-0.29515 -0.51031,-0.51031 -0.0761,-0.15215 0.0761,-0.35817 0,-0.51031 -0.10758,-0.21517 -0.40273,-0.29514 -0.51031,-0.51031 -0.0761,-0.15215 0.0761,-0.35816 0,-0.51031 -1.36082,-2.72165 0.34021,1.36083 -1.02062,0 -0.24056,-0.24056 0,-0.68041 0,-1.02062 0,-0.1701 -0.1701,-0.51031 0,-0.51031 0.17011,0 0.17011,0.51031 0,0.51031 -0.38036,0 -0.75166,-0.24135 -1.02062,-0.51031 -0.12028,-0.12028 0.39003,0.12028 0.51031,0 0.12028,-0.12028 0.17011,-0.51031 0,-0.51031 -0.24056,0 -0.26975,0.51031 -0.51031,0.51031 -0.1701,0 -0.16137,-0.45651 0,-0.51031 0.48412,-0.16137 1.02062,0 1.53093,0 0.51031,0 1.02062,0 1.53093,0 2.21134,0 4.42268,0 6.63402,0 2.72165,0 5.4433,0 8.16495,0 1.36082,0 2.72466,-0.0905 4.08247,0 1.20015,0.08 2.37533,0.39063 3.57217,0.51031 0.50777,0.0508 1.02062,0 1.53093,0 0.85051,0 1.70103,0 2.55154,0 2.21134,0 4.42268,0 6.63402,0']

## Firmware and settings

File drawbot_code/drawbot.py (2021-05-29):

import time

import hatched
import numpy as np
import serial
import tqdm

from optimize import optimize_ordering
from preview import preview_drawing
from utils import *


from shapely.geometry import MultiLineString


#############
# Constants #
#############

STEPS_PER_MM = 20
WIDTH_MM = 62
HEIGHT_MM = 225
WIDTH_STEPS = WIDTH_MM * STEPS_PER_MM
HEIGHT_STEPS = HEIGHT_MM * STEPS_PER_MM


def main():
    # Get lines to draw
    print('Converting image to lines...', end='', flush=True)
    # Some pretuned images and parameters as examples
    params = [
        dict(file_path='imgs/skull.png',
             hatch_pitch=5,
             levels=(24, 80, 128),
             blur_radius=15,
             invert=True),
        dict(file_path='imgs/lines.jpg',
             hatch_pitch=4,
             levels=(240, 240, 240),
             blur_radius=0),
        dict(file_path='imgs/lenna.png',
             hatch_pitch=2,
             levels=(102, 148, 200),
             blur_radius=8),
        dict(file_path='imgs/helloworld.png',
             hatch_pitch=5,
             levels=(24, 80, 130),
             blur_radius=15,
             invert=True)
    ]

    # Converts an image to line drawing with diagonal hatching
    # Play with levels parameter and blurring to get right
    # Will error if contours too complicated
    mls = hatched.hatch(**params[3], save_svg=False, show_plot=False)

    mls = mls_normalize(mls) # put lines in unit square
    lines = list(mls_to_lines(mls)) # convert to simple list of list of points

    # Greedily sort the lines in an efficient order
    lines = optimize_ordering(lines)

    print('done')

    # Preview what the drawing will look like
    preview_drawing(lines, speed=0, draw_movement=True, animation=False)

    # Convert to motor commands
    cmds = lines_to_motor_cmds(lines)

    # Connect to drawbot 
    print('Connecting to drawbot...', end='', flush=True)
    arduino = arduino_connect(port='/dev/cu.usbmodem14401')
    if not arduino:
        print('fail')
        return
    else:
        print('success')

    # Send motor commands
    cmd_counter = 0
    for motor1_steps, motor2_steps, draw in tqdm.tqdm(
        cmds, desc='Sending motor commands', unit='cmds'
    ):
        # Send the command
        arduino_write_cmd(arduino, motor1_steps, motor2_steps, draw)

        # Wait for confirmation
        cmd_num = arduino_read_int(arduino)
        #assert cmd_num == cmd_counter + 1, cmd_num

        cmd_counter += 1


def arduino_connect(port, baudrate=115200, timeout=5):
    arduino = serial.Serial(port=port, baudrate=baudrate, timeout=timeout)
    time.sleep(3)
    
    arduino.write(bytes('ready', 'utf-8'))
    time.sleep(0.05)
    
    res = arduino.readline().decode('utf-8').strip()
    return arduino if res == 'ack' else None


def arduino_write_cmd(arduino, motor1_pos, motor2_pos, draw=True):
    msg = ','.join(['1' if draw else '0', str(motor1_pos), str(motor2_pos), ''])
    
    arduino.write(bytes(msg, 'utf-8'))
    time.sleep(0.05)


def arduino_read_int(arduino):
    res = arduino.readline().decode('utf-8').strip()
    print(res)
    #return int(res)
    return res


def lines_to_motor_cmds(lines):
    def to_cmd(a, b, draw):
        dx = b.x - a.x
        dy = b.y - a.y

        assert -1.0 <= dx <= 1.0, (b.x, a.x)
        assert -1.0 <= dy <= 1.0, (b.y, a.y)

        x_steps = dx * min(WIDTH_STEPS, HEIGHT_STEPS)
        y_steps = dy * min(WIDTH_STEPS, HEIGHT_STEPS)

        motor1_steps = x_steps + y_steps
        motor2_steps = x_steps - y_steps

        return (motor1_steps, motor2_steps, draw)

    cmds = []
    prev = Point(0, 0)
    for i, line in tqdm.tqdm(
        enumerate(lines), desc='Converting lines to motor commands', unit='lines'
    ):
        if prev:
            cmds.append(to_cmd(prev, line[0], draw=False))

        for i in range(len(line) - 1):
            cmds.append(to_cmd(line[i], line[i + 1], draw=True))

        prev = line[-1]

    return cmds


if __name__ == '__main__':
    main()

    exit()
    
    # Some pretuned images and parameters as examples
    params = [
        dict(file_path='imgs/skull.png',
             hatch_pitch=4,
             levels=(24, 80, 128),
             blur_radius=15,
             invert=True),
        dict(file_path='imgs/lines.jpg',
             hatch_pitch=3,
             levels=(240, 240, 240),
             blur_radius=0),
        dict(file_path='imgs/lenna.png',
             hatch_pitch=2,
             levels=(102, 148, 200),
             blur_radius=8)
    ]

    # Converts an image to line drawing with diagonal hatching
    # Play with levels parameter and blurring to get right
    # Will error if contours too complicated
    mls = hatched.hatch(**params[1], save_svg=False, show_plot=False)

    mls = mls_normalize(mls) # put lines in unit square
    lines = list(mls_to_lines(mls)) # convert to simple list of list of points

    # Greedily sort the lines in an efficient order
    lines = optimize_ordering(lines)

    # Preview what the drawing will look like
    preview_drawing(lines, speed=0, draw_movement=False, animation=False)

    # Turn coordinates into proportional displacements and distances for robot
    # also includes whether drawing or not
    start_point, info = lines_to_robot_info(lines)
    
    # Here's an example of how you might use info:
    # distances are normalized for unit square
    # This info should be precomputed with hardcoded motorspeeds and scale
    WIDTH = 30 # cm
    HEIGHT = 30 # cm
    SCALE = min(WIDTH, HEIGHT)
    MOTORSPEED = 10 # cm/s

    # Assume these methods exist
    move_to_start = lambda start_point: None # easy if arm boots up at 0,0
    raise_pen = lambda: None
    lower_pen = lambda: None
    set_motor_x_speed_for_seconds = lambda speed, seconds: None
    set_motor_y_speed_for_seconds = lambda speed, seconds: None

    move_to_start(start_point)

    with open('output.txt','w') as f:
        for dx_norm, dy_norm, dist, draw in info:
            if draw:
                lower_pen()
            else:
                raise_pen()
                print('here\n')

            seconds = (dist * SCALE) / MOTORSPEED

            motor_x_speed = dx_norm * MOTORSPEED
            motor_y_speed = dy_norm * MOTORSPEED

            set_motor_x_speed_for_seconds(motor_x_speed, seconds)
            set_motor_y_speed_for_seconds(motor_y_speed, seconds)
            f.write(str(dx_norm)+ ", " + str(dy_norm)+ ", " + str(dist)+ ", " + str(draw)+ '\n')

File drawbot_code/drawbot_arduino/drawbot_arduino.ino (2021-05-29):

// 
// IMPORTANT: Assumes pencil is in start position
//

#include <AccelStepper.h>
#include <MultiStepper.h>

// Pins for motor 1
#define STEP_PIN_1  3
#define DIR_PIN_1   4

// Pins for motor 2
#define STEP_PIN_2  12
#define DIR_PIN_2   13

// Initialize individual steppers
AccelStepper stepper1(AccelStepper::FULL2WIRE, STEP_PIN_1, DIR_PIN_1);
AccelStepper stepper2(AccelStepper::FULL2WIRE, STEP_PIN_2, DIR_PIN_2);

MultiStepper steppers;

long positions[2];  // Array of desired stepper positions
bool draw; // Whether to draw (pencil down) or not

unsigned long commandsRun; // Number of commands successfully run

void setup() {
  Serial.begin(115200);
  Serial.setTimeout(5);

  listenForPythonScript();

  // Configure each stepper
  // TODO: do speeds do anything?
  stepper1.setMaxSpeed(800);
  stepper2.setMaxSpeed(800);

  // Combine the steppers in a MultiStepper to drive simultaneously
  steppers.addStepper(stepper1);
  steppers.addStepper(stepper2);

  commandsRun = 0;
}

void loop() {
  draw = readCmd(positions);
  // TODO: move up or down

  // Adjust target positions to current positions
  positions[0] += stepper1.currentPosition();
  positions[1] += stepper2.currentPosition();

  // Move the motors
  steppers.moveTo(positions);
  steppers.runSpeedToPosition(); // Blocks until all are in position

  // Let Python client know command finished
  Serial.println(++commandsRun);
}

//
// Utility Functions
//

bool readCmd(long positions[2]) {
  while (!Serial.available());
  int draw = Serial.readStringUntil(',').toInt();
  positions[0] = Serial.readStringUntil(',').toInt();
  positions[1] = Serial.readStringUntil(',').toInt();
  return draw == 1;
}

void listenForPythonScript() {
  while (!Serial.available());
  String recv = Serial.readString();
  if (recv == "ready") {
    Serial.println("ack");
    return;
  }

  // Stall forever, connection failed
  while (true) {
    delay(60000);
  }
}

void waitForInput() {
  while (!Serial.available());
  int throwaway = Serial.read();
}

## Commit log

2021-05-29 initial upload
    [Back_pulley.stl, GT2_Pulley.stl, GT2_belt_clamp.stl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]
2021-05-29 drawbot code
    [pyvenv.cfg]
